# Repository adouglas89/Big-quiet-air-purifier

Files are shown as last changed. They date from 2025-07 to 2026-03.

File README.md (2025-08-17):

# Big-quiet-air-purifier
Big Quiet Air purifier/filtration machine, can be remotely managed/monitored, very high performance to cost ratio.
This uses a large axial fan with unprecedented flow to noise ratio at the pressure of concern - about 4-6 pascals, which is not much pressure.  It also gets relatively good flow at higher pressures for the noise, but you want to keep in this region if you can for highest CADR.

This system uses standard furnace filters, which are available in a wide range of MERV ratings, and even HEPA, in the same size and shape.  You can sub in whatever you want but probably there is a MERV rating that gives the best CADR.  It may or may not be MERV-13, but that's a good starting point.

The fan currently requires a large format printer.  Don't buy anything Tronxy, I can tell you that, they are the worst machines I have ever encountered and the company won't send you spare parts etc either.

Everything in this repository is going to go out of date as things are changing fast.

Actually making one is something that will become easier as the development is sorted out better.  If it's confusing that's no surprise, manufacturing is never easy, people don't respect it for some reason but they should.

The CAD files for the big quiet fan will also be integrated into this CAD file from now on.  The files in the repository specifically for the big quiet fan will eventually be obsolete unless I update them.

here is the bom: https://docs.google.com/spreadsheets/d/1DK419Db4-yF4lkq_DYZrtrG0oX9ysA3eVCCv0GqU3Kw/edit?usp=sharing
it is changing rapidly so I don't really want to upload it as a static document, and there seems to be no way to have a spreadsheet on github.  When things stabilize I will put it here.

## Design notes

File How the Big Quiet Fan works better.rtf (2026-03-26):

This document is to answer the often asked question of how/why the big quiet fan is so quiet.
● First of all the actual details of curves and polymers are not the whole story
○ The incentives surrounding the project
■ Lack of asshole boss rushing me
■ My own desire to make stuff that’s really really quiet, and do a good job to prove my abilities in this regard. I want it to be beautiful.
■ My reputation in the community and with the funding organization was an important motivating factor I guess.
■ A focus on sheer performance rather than appearance or manufacturability in the early stages. In fact sometimes noise is considered beneficial because people perceive something that’s louder to be more powerful. Obviously dispensing with that kind of pandering to ignorance is an easy way to make progress on performance. I also rejected the idea that it must be cheap. The *ratio* of cost to performance is much more important. In a way both of these and much more comes to making a wise objective function early on and allowing that to guide development efforts. The whole thing is one big optimization effort.
○ The methods I have employed including optimization, actually building prototypes, working with good efficiency are important. Both in terms of getting on with things faster and sooner and also with less money and space. With a fixed budget, higher efficiency will give a better result.
■ Prove the most uncertain stuff first. That was the blades and then the ability to print them with reasonable efficiency. Then the motor/driver comes after. That way if you have to change course you have less lost effort.
■ Obviously basic engineering fundamentals apply, like using modules that others have done a reasonable good job on wherever they are adequate.
○ “Forever modular” is useful, keeping the door open to improvement well after I thought I was done.
○ Keep orderly notes and data, I don’t think paper notes are really up to the challenge. You can’t make a spreadsheet on paper. This is important to remember and refer to what worked best, so you can mix and match the best features during the optimization process. And also if something goes wrong you can figure it out better.

I also spent some time relatively poorly, because I was working towards serial production through additive manufacture. So this whole project did take longer than it would have if I had been able to plan ahead a little more effectively. However to be fair I see supposedly much more experienced people doing very similar things with far lower efficiency. Also exploration is kind of like that, you can’t know what’s ahead, that’s part of the program.

One thing that was profoundly missing was collaborators. That would have helped a lot. Except the funding was in a way a form of collaboration.
This could have been done in some kind of community space, but you’d need some space of your own, and the freedom to run the machines overnight etc. Being able to work in my home was useful on a technical level but I think quite a problem psychologically, as you tend to have problems sleeping and waking when working and sleeping in the same relatively small house (even a full sized house, which I had for a while).

It would be a good idea to also discuss what did not work out as well, some of this will be implied, some included after.

Some people will say this is too much detail, but when you go to make a variant, it’s not going to be too much.

What is the general technique employed here?
● The general idea is to first do the best we can with simulations, then build a test rig and then try various fans with a reasonably intelligent approach (better than brute force) to see which gives the best noise and flow/pressure. To simplify things, I picked one RPM, 300, and optimized to get better results at that point. Now I’m usually using 400 rpm because it’s quiet enough at that speed, so optimizing again for that RPM might yield improvement. Unfortunately this is not actualy that easy as the only practical way to know how much noise one aspect is contributing is by eliminating it. So the motor for instance, you have to make that quiet before you can get far on the blades.
○ The optimization process involved binary searches and also looking in there with smoke etc. to see how the air was flowing around, listening to see if I could determine how the noise was being produced (easy to tell motor hum or blade buzz from the whoosh of the blades due to turbulence for instance). Then forming hypothesis, proving them and testing more.
○ I make at least 52 unique prototypes, I think. Some were not documented as they were uninteresting, like the one with the slightly defective frame that made a surprising amount of noise as a result. By this I mean I often recycled parts to make new fans, including mixing various primaries and secondaries to see what worked better. Different spacings between primary and secondary were also tried but I’m not including that in the total of 52. There must have been hundreds of exact unique combinations tried. The most important thing to document is when progress is made, but documenting everything is probably a good idea, as long as you can still find the good stuff.
○ Obviously, back the best stuff up periodically and keep an orderly workplace etc.
● It’s also useful to note that MERV-13 filters may not be the optimal at these pressures and for these configurations. There may be a significantly better filter/geometrical arrangement combo. You’d have to go back and forth testing and improving both to work your way to a better air purifier if you wanted to optimize for both 400 rpm and different filters. I used 10x merv-13 filters with the VVV in the middle (see bqap builds document).
● A primary blade that is relatively thick. It imparts pressure to the air, and also rotational motion. The pressure is directly useful, the rotational motion will be converted to pressure to some degree by the secondary. Usually it’s just about pressure. The thicker the blade disk (the cylinder around the blades) the better this works, but of course it’s a practical compromise with how large you want to let them be.
● A secondary blade, also called stator blades, which are stationary but the air is rotating relative to them, at a lower rpm however, than the primary relative to the air entering the fan.
● The primary and secondary are curved oppositely to each other, that is the spiral in the xy plane is opposite handedness. This prevents the pressure wave emanating from the primary from slamming into the secondary all of a sudden, which produces a buzzing noise that we don’t want. Many fans use struts that curve for this reason.
○ The struts on some blades are also flat and slanted to reduce their cross section in the direction which the pressure wave propagates. The secondary blades are to some degree like this automatically, although they can’t be minimal cross section of course. But they are a lot better than flat bars.
● The blade number and curves of the primary and secondary are different, the de facto rpm is different so the optimal isn’t likely to be the same.
● Spacing between the primary and secondary turned out to be important. Early prototypes did not work well as the spacing was too large.
● The thin wall on the outer edge of the blades is not strictly that helpful from a noise standpoint, I think, but it is important structurally, allowing the blades to be thinner, and thus easier to print and mold. It also prevents them from flapping around, but to be honest I never tried any variants without it so I don’t know the impact it’s having for sure. People think it reduces tip vortices, but I don’t think that’s likely to be a major factor here, that’s more of an issue at higher blade velocities.
● The spiral curvature (xy plane) and zy plane curvature of the blades,blade number for both the primary and secondary, thickness of the blade disk (thickness of the cylinders that surround the primary and secondary blades), hub diameter had to be adjusted to find something reasonably close to optimal. Diameter was fixed but in another application you might want to optimize that too.
● The grille has to be adequately far away from the primary blades, otherwise it creates noise as the pressure waves slam into it. This is why it’s not directly against the secondary, or integral with the secondary. I found it had to be a separate component, which is unfortunate as it costs more. Of course it can’t be too dense/thick elements as that would impede airflow, too. Making it further away from the primary also reduces the density it has to have, allowing air to flow through it better.
● The polymer turned out to be important. By coincidence I found some fans were quieter than others, and since I kept good notes (this is important, keep orderly notes and data) I was able to identify that it was the polymer used.
● The motor/drive solution:
○ After realizing that stepper motors do actually have the required speed/torque characteristics, which is hard to get from other motors at a good price, I pursued the use of a stepper motor as a practical power producing motor
○ The previous motor was an 11 pole pair motor. A typical stepper is 50 pole pairs. They are also bipolar rather than three phase. Aside from this, driving them and their noise characteristics don’t have to be that different
○ Everyone thinks steppers are inherently noisy and this is not entirely wrong, because of the high pole pair count. However whichever motor I use I would probably want vibration isolation, so if I have to isolate the stepper motor this isn’t that big a deal.
○ After realizing the drive strategy was working particularly well, I tried to eliminate the buzzing noise with anti cogging. This did not go well. I spent along time on it and got basically nothing for it. It is not clear to me why it seems to be practically impossible to drive the motor with very little torque ripple. I think it may involve some kind of excited oscillation. There seems to be no electrical waveform that can be fed to the motor that leads to completely smooth motion.
○ Therefore I decided to just suspend the motor so it can produce torque but the vibration is isolated. This is inconvenient and adds cost, but again probably any motor would require something like it to some degree. Going to town with it is not a whole lot worse than a little bit.
○ The motor turned out to vibrate due to some kind of feed back loop combined with some harmonic resonance. It was so severe that when allowed to vibrate due to the decoupling, it would stall at some speeds. To dampen this, I added a flywheel made of a high damping polymer, 95A TPU. I had some difficulty getting it to transmit enough torque, but eventually solved that. This appears to reduce the oscillations at an even lower level. This is what makes me think there is some kind of oscillation that is excited and part of a feedback loop. I’d have to figure out the physics and math out a bit better to elucidate this (see where the gain coomes from eetc by modelling the system basically), but for now it works fine.
○ The drive strategy is particularly curious. It’s not actually open loop as we know it, there is no actual current regulation. It’s only ramped voltage. It works because the back emf goes down when the torque angle increases, which it increases with load. If we apply a constant RMS voltage, thus the current actually compensates for higher load automatically. It just has to be in a suitable range for the rpm. It could almost work without this, but having it is particularly helpful as it further increases safety margin against stall.
■ There is a system in the driver for the more recent programs that uses a polynomial that predicts (measured) normal operating current. If operating current is outside the range predicted, it shuts off themotor. You have to power cycle it to resolve the situation. In other words you need the user to come pay attention, which is what we want. If someone shoves something in the fan, it therefore shuts down automatically. If it stalls for any reason like a wiring error, this system also trips.
■ Thi strategy is mentioned in some old textbooks but I haven’t sen it anywhere else. I would simply describe it as voltage ramped synchronous drive. Not open loop, open loop implies current regulation most of the time.

It’s worth noting that it’s probably possible to improve performance slightly further by further adjusting the curves and blade number, thickness of the blade disk, hub diameter etc.I am not immune to the reality which probably led most other fans to not be very good, which is that you have to get on with actually making them at some point, and there is not really that much good reason to exceed the requirements set. That would be ASHRAE 241 for the amount of clean air we need in a classroom and other buildings,and ANSI S12.60, for noise in classrooms (hospital wards and other spaces have similar standards which have mostly similar values anyway). This fan can already be used to make an appliance that can do that with only one fan, while everything else is a long way away from that.

Because things are modular I could change things later to pursue this improvement, if/when there is a good enough reason and funding.

What did not work very well?
● The rings similar to the outermost wall, I had some in the middle regions too, and they added a lot of noise. They did improve the flow/pressure to rpm ratio, though, as predicted by simulations. I noticed from the simulations that the pressure/flow was better in the regions close to these rings, so that is why I added them. That was correct. But the simulation did not show the increased noise.
● I tried using a tpu/nylon blend to increase damping, just for the primary, but it made no difference so I went back to the previous approach. I thought it was going to help as the difference in damping between some rigid filaments did help. It might help for the secondary more, but it’s a little too floppy, it was 72D durometer. 100D might work ok but I couldn’t get any. You can have high damping while still having high stiffness, there is nothing stopping that. It’s just that TPU has good damping and is usually used in elastomers. There are some papers that describe filaments with unusually high damping but you can’t buy the filament of course.

Things I did not try
● Multiple rotors, separated by stators to reduce the rotational velocity of the air. This would increase cost and it actually can get complicated because the bearings can make noises etc. which can be solved but it takes more time and the per unit cost would go up. A single primary and secondary is a reasonable compromise.
● One thing that has some potential is airfoil shaped blades, i.e. the back of the blade has a different curvature than the front. This would be easy to do with printing but it makes the blade thick so with molding you’d end up with heavy blades and using a lot of plastic. Contraction could also be a serious problem. You could try to make it in pieces and assemble them or something. But that’s expensive. For this reason I did not explore airfoil shapes much. I did simulate some and it didn't seem to help much so I didn’t pursue it.
Things that probably don’t matter much
● Some people think the ridges on the sides from the printing must have an impact that is detrimental. I think this is unlikely due to the boundary layer, especially.
● I tried slanting the outer wall a little but it made basically no difference. I may do this again when designing for manufacture as it should make removal from the mold easier.

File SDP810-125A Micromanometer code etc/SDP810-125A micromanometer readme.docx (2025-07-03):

Check out the datasheet for the sensor, it says it’s pretty good.

Shop around before you buy, some places have it a lot cheaper, like half the price of others.

This is a simple system to read the sensor over I2C a bunch of times, then calculate the average and display it on an LCD.

It’s made for a raspberry pi pico. You will find the pin numbers in the code, remember they are GPIO numbers not physical pin numbers.

Note that the sensor actually has a small hole from one side to the other, this is a very important thing to know, because if you use a long thin tube to the sensor, the apparent pressure will be reduced. It remains largely linearly proportional to the real pressure but you gotta be aware of this phenomena. If you want a good reading use a short wide tube on the sensor side. A 380 mm long 1 mm ID silicone tube reduced the pressure reading by a factor of 3.5, approximately.

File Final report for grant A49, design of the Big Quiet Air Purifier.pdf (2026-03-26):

# Final report for grant A49, design of the Big Quiet Air Purifier

Overview:
This project went well as far as it was taken, however we terminated it early to roll the funding that remained into the Big Quiet Fan mass production. This is because it became apparent that the taped together air purifiers actually work quite well, and the other aspects that differentiate a BQAP from a taped together assembly (which I dub an Extra Quiet CR box or EQ-CR box) are not really that important, but at the same time are costly.

However, the anemometer and the internet of things control box were a good success. Secondly, I did learn a lot which I do plan to eventually hopefully apply to build additional prototypes, and if the market is amenable, to sell alongside the big quiet fan, however it doesn’t look like a low hanging fruit.

One finished air purifier is now in operation in a classroom at the University of Waterloo. A second one is a Cite Des Hospitaliers, a coworking space, in Montreal. A third is at Foulab, a hacker space in Montreal. A fourth was located at a social central called Lachoppe, but they foolishly threw it in the trash, an absurd thing to do, illustrating that the machine alone will never be enough, anti-propaganda is important as well.

The school board of Connecticut has apparently funded taped together CR boxes for all it’s 40,000 classrooms, at about 11.5 million USD or something, so apparently taped together boxes are adequate even in that sensitive context. Thus, focussing on the fan seems like a good first step.

I developed solutions for the physical structure, holding filters of various sizes with the same physical structure, and getting a large number of filters integrated into the machine to reduce pressure drop. I developed the 6 filter internal V box, which nobody else seems to have thought of before but works well, and is in general the winning configuration. Even a good solution for the handles at the corners is done.

I hope to use extruded aluminum in the future as the wood was of marginal strength and appearance.

I realized that because of how the details stack up, adding more filters generally decreases the cost per cubic meter. I realized cost per cubic meter is a good way to think about things.

I developed a good approach to a cosmetic cover, and have ideas to improve it further. Solutions for tamper proofing were also found (durable yet low cost grilles and also mounting it high up). I have ideas for putting the fan in pushing mode to further increase CADR and mounting it near the ceiling to leverage displacement flow.

Concepts for embedding the whole system in a false ceiling are interesting.

Budget:
Total budget was $30,000. Not quite all of this was expended. This may indicate that it would be a tight squeeze to make 30 units. However the plan was supposed to be to actually sell the units so that part would have been mostly self funding. I think I struck a pretty good balance.
| CAD | USD
labor cost | 25060 | 18159.4202 9

sum of all
costs with
labor | 31072

22515.9420
3

Estimated impact
The designs are published, as well as some information about the general lessons learned. The filter configuration with the diagonal internal V and 6 filters is applicable to taped together boxes, allowing increased performance while also reducing cost.

Once we have a good supply of the critical ingredient, the fans, it will be time to pick this up again, or perhaps someone else will. There are a number of examples of entrepreneurs making kits for air purifiers, and this both builds upon and enables that further. I have offered Northbox a sample control box and anemometer assembly so he can make his air purifiers remote controllable and monitorable (including the filter cloggage levels).

Many users will not be happy with taped together CR boxes, so this is a good start on a good option with the same net performance, albeit at a higher upfront cost, and with the same great low running costs. Filter changes are easier and the finished assembly may be possible to get UL listing for, encouraging uptake in hospitals and other tightly regulated spaces.

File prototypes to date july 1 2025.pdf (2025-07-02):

# 10 Filter filter box (“CR box”) with Big Quiet Fan experiment/mock up(s)

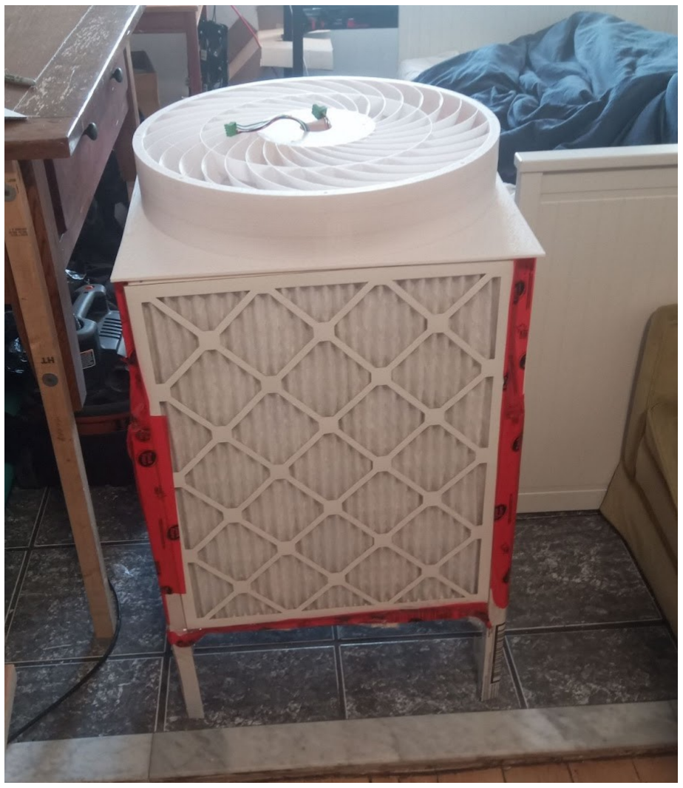
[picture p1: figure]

Update march 5 2025: This device uses an older model of fan. Considerable progress has been made. It’s been in operation all this time and working well. I added a safety feature, a thermal switch, but it hasn’t tripped even at full power. During summer at high ambient temperatures that could still happen. The safety margin is a bit slim on that count, but the safety margin against actual overheating is good. Remember this is all only proof of concept, mostly about the blade design and the filter arrangement, to prove high CADR to noise ratios and high cubic meters of air to total $ expended (10x or more higher than the next best, 30x or more than typical air filter units). Also the estimates for the boxes in this document may not be very good, regarding flow rate etc. There were a lot of sources of error back then, they were only estimates. These filters are also on the crummy side, lower flow rates than filtrete ones. I have since build a better box and it works well. I will build another in due course, but I may return to these crummier filters because they are half the price and that’s pretty important. I have also measured a very similar system precisely with a validated anemometer. The latest fan gets 1452 CFM measured precisely with the validated anemometer, at full speed, 400 rpm (47.5 dBa) with 3m filtrete merv 13 filters, and 1111 cfm at 300 rpm (37.5 dBa). That’s flow, not cadr.

Edit: to be clear, this fan is 3d printed. It’s source, the cad files, are available at openerv.ca as well as information to help you get the rest sorted out. However it unfortunately requires a large format printer. Don't get the veho-600 it's terrible, or anything tronxy. The orangestorm from elegoo looks good.

# Intro

I have been working on a window-fan sized fan with the best flow to noise ratio through a set of merv 13 filters I was able to arrange reasonably, as a proof of concept that it’s possible and practical to do far better than we have been doing.

I also thought up a way to cram 10 filters into a filter box of nearly the same dimensions as a 5x or 4x box. It has to be lifted up off the ground with legs, like a 5 filter box, rather than sitting on the ground, but that vertical space is not usually used anyway.

The sides should stick out a little more than a 4 filter box, just a few centimeters on two of the sides, to improve flow on the interior of the box. I just made it a square instead, so it sticks out on all sides, to keep it simple.

Edit: move the triple V down some too, that should help.

You might even be able to up it to 12 filters with a quad V.

The key to realizing why this is a good idea is that the cost per cubic meter does not go up when you use more filters, because you get x amount of air per filter before it’s “clogged” either way. Or rather, X amount of particulates, and the air passing through in this context has already passed through and thus has very little particulates in it.

But when we have more filters, we can turn the fan down and get less noise for the same flow rate. Efficiency of particle removal might even go up as velocity through the filters goes down. The fan can be lower power, which is cheaper. Fitler changes are less frequent because each filter captures a lower fraction of total particles the machine intecepts. It’s definitely a win, except that the upfront cost is of course higher for the larger number of filters. Except now we can use cheaper (about half the price) generic filters instead of the good Filtrete ones or whatever, and still get pretty good performance (the cheap ones do have about 1.5 times the pressure to flow ratio). Also sourcing filters becomes easier for a given performance.

Edit Dec 10 2024: Actually, I think the cost per cubic meter may actually go down when we add more filters. This is because you have a pretty high ACH with these appliances, thus almost all the particulates that can clog the filter have already been removed from the air that passes through the appliance. It’s about the particulate matter the filter intercepts, not the amount of air that passes through it, that determines how long the filter lasts before it must be replaced (assuming a given flow reduction is acceptable). But because the particulates released into the room to do not increase when we filter the air at a higher ACH, that additional ACH is relatively cheap - nearly free probably - in terms of filter cloggage/cost. Secondly, though this is not additive or multiplicative with that but could become prominent in some contexts: suppose you need a CADR of X. You can get more particulates intercepted per filter if you have more filters, because each one can clog more before it passes the “time to replace it” threshold, because the sum of all the filters flow is the cadr. Thus if you have twice as many filters, each one can suffer twice the cloggage level (half the pressure to flow ratio) and still be serviceable in an appliance that gives X cadr. Thus, you can extract more filter life per filter if you have more filters, all else being equal. Thus, the cost per particle intercepted or per gram of solid matter removed, actually may go down with more filters, all else being equal.

So, increasing the number and density of filters is really the way to go, pretty much a win all around, all else being equal it’s going to make things cheaper and quieter for sure, the only downside is it increases the sticker price of the assembly, course. If we assume a certain interest rate on the cost of the filters because we need to buy them today rather than in a year from now, the cost of the expenditure is very small compared to the benefits that accrue along the way. It's a very good investment. So rationally, it's really the way to go. Exactly how much so warrants a spreadsheet to reckon.

You want to try to use the wells-riley equation and some similar approximations to calculate the cost per infection prevented for various appliances. The cost will change for different contexts though. What we really want is an objective metric that calculated the cost per qaly gained, with weighted average calculated for a wide range of scenarios the particular machine is intended for. You would subject each machine proposed to this evaluation and pick the best. I think this fan combined with very dense large filter like this would likely be a winner by a large margin but it would be nice to actually check this quantitatively.
– end edit

In the case where you simply tape together 10 filters, it has the added benefit, and also in other cases, that you, at a flow rate of X, do not need to change the filters as often. Indeed <1/(2.5) times as often, as compared with a 4x box, if we assume they need to be replaced after each filter intercepts x many grams of particulates, and total particulate interception rate is
unchanged. We may get more than that because the particulate loading per filter that is acceptable may be higher in this 10x config. Since we have to tape together a new box every time, we’d appreciate this long lifespan. Estimating filter life is difficult but some studies indicate a 4x box had no problem after a year of continuous operation so we might get like 3 years, I don’t know. The degradation of the electrostatic media could be a factor at that time scale. What we would ideally talk about is grams of particulates intercepted vs the CADR the appliance gets, and then have a cutoff at say 30% reduction from the new state and see how many years that is. Then we could compare various configurations more directly and reliably.

This box is a big one but the concept can just as well be applied to smaller boxes, you can get filters down to 8 inch size even.

The key is the triple V in the middle, you might even be able to make it a quad V, but I figured this was a good start.

When using crummy generic filters like these, it is particularly valuable, as they impede the airflow considerably more than good quality filters.

I have estimated the airflow with my Big quiet fan, by covering most of the filters, to increase the pressure, measuring the flow rate through the filter with my anemometer, calculating the CFM per pascal, and then extrapolating to the situation with 10 filters uncovered (the pressure is also measured with the same sensor in the 10 filter context).

The net flow rate indicated by the instruments was 1475 CFM. If the efficiency is 0.8 then we get a CADR of 1180 CFM. With a noise of 40.6 dBa, according to prior measurements of the fan at the same RPM (300 rpm). However I suspect my anemometer may be reading a bit on the high side. I am looking for someone with more sophisticated test equipment.

It occurs to me you could replace one side with another fan. Basically you are condensing 2 to 2.5 filter/cr boxes into one, approximately. Not a bad trick really.

Steps:

First we are going to make the legs out of cardboard. I tried to make them right angle triangles but my precision was a bit poor and I think square might be better. Cut strips of cardboard about 500 mm long and 15 cm wide. Then fold them along the corrugations at three lines spaced equally apart with a straight edge, and tape them. I forgot to take pictures of this step but it’s pretty straightforward. Mark the stuff with a straight edge and

marker then cut with a box cutter.

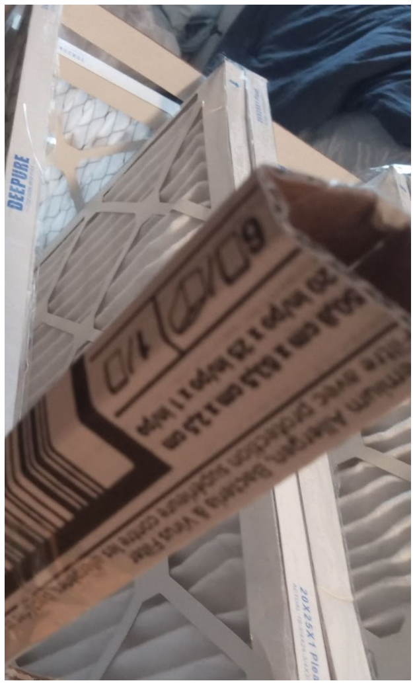
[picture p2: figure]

Mark the legs at about 200- 250 mm, but all in the same position from their ends, with the marker, we will use this to help position them later
Tape the peripheral box together, I went around with the tape, attaching the filters and legs at each corner successively. It helps to put a bunch of tape pieces on a nearby table so you can hold stuff with one hand and grab tape with the other. Don’t worry about sealing anything yet, we get the structure together first and then we seal stuff.

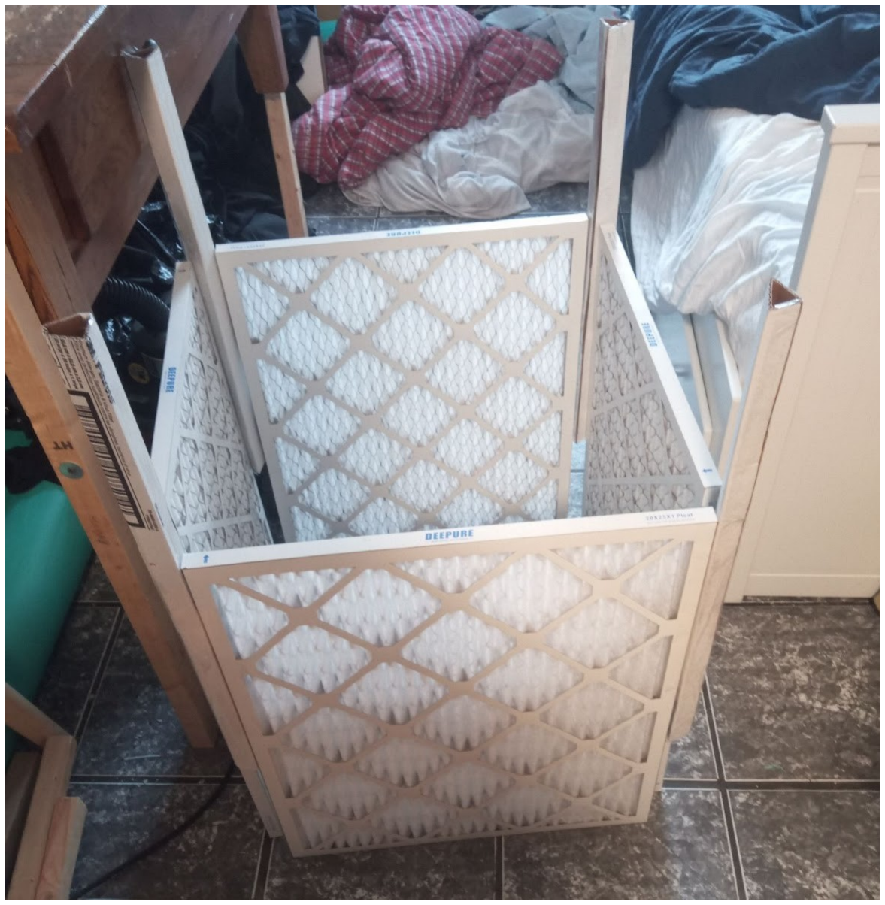
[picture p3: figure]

Next, we need to prepare the triple W insert. Start by arranging the filters in the right way, the arrows to indicate direction of flow should be right. The outer two point outwards, then the ones in between alternate.

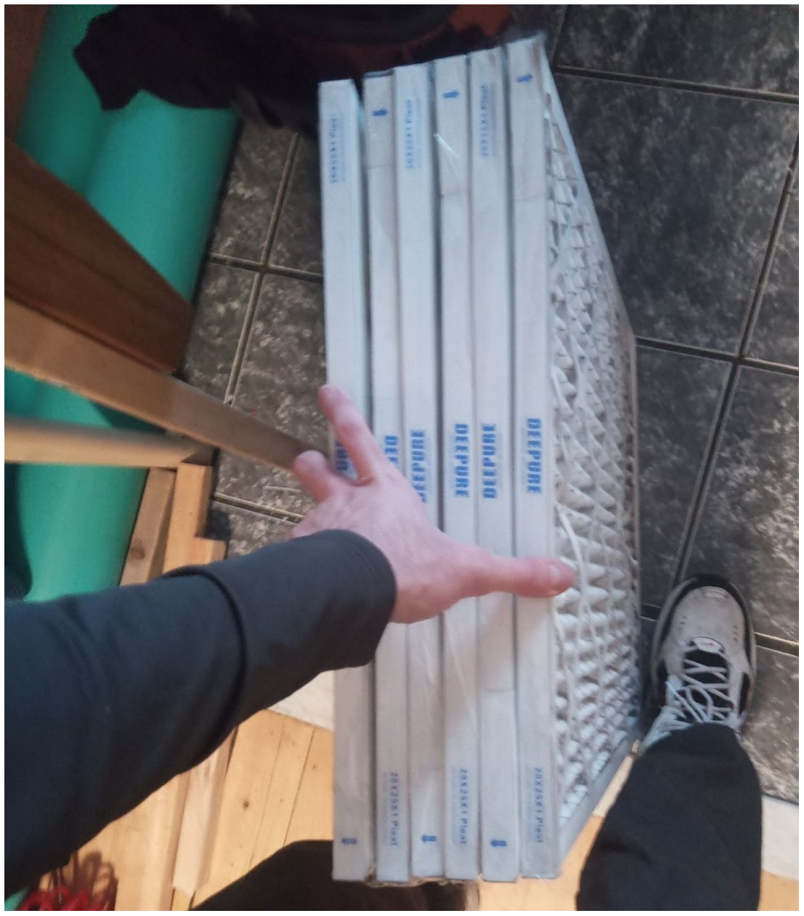
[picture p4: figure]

Just tape all the edges together, don’t worry about which ones to tape and which ones not. The edges of the tape stick anyway. Just tape it all up and then cut it in the right places with a box cutter. I then attached some strips of cardboard to hold things in position. Measure it against the nearby square box thing to make sure the VVV is the

right width etc.

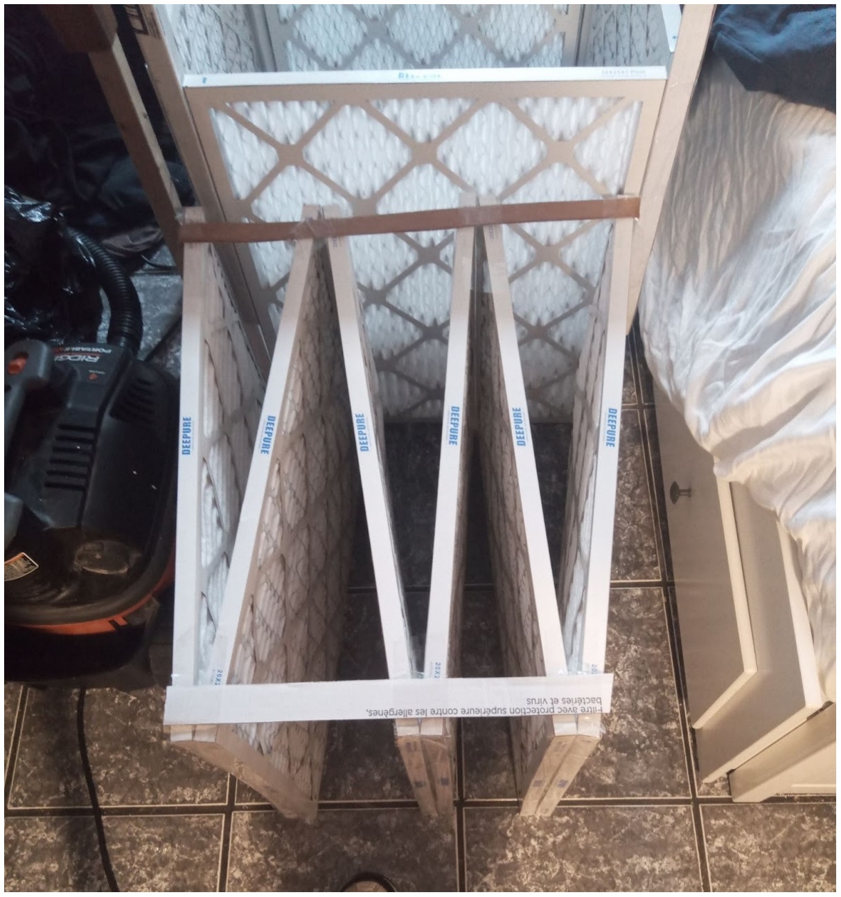
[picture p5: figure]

Next we block off the relevant areas in the Vs with tape. On the wide end it’s going to stick out so the tape doesn’t have to extend to that area

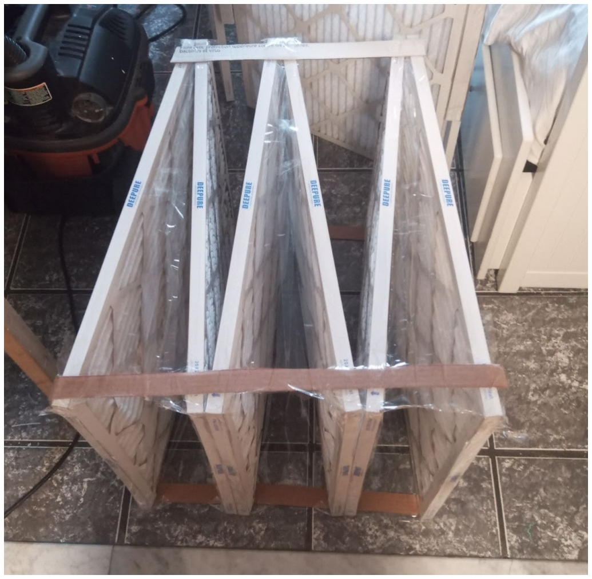
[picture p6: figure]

Now we can insert this component into the peripheral box to make sure it fits. But we want space at the end for air to flow, so I’m going to back them out a bit, whether this is necessary I don’t really know.

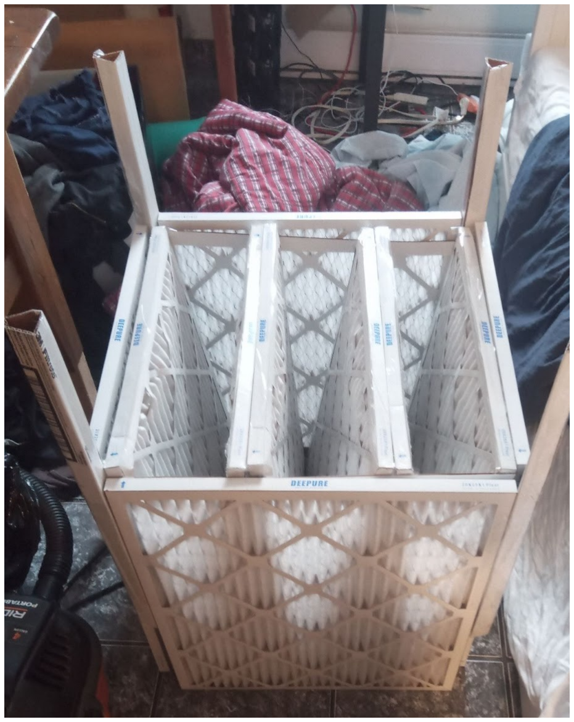
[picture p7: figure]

Tape the triple v thing in position and then seal around it. *notice that it is not flush with the bottom of the peripheral filters*. This extra space is important for air to flow around.

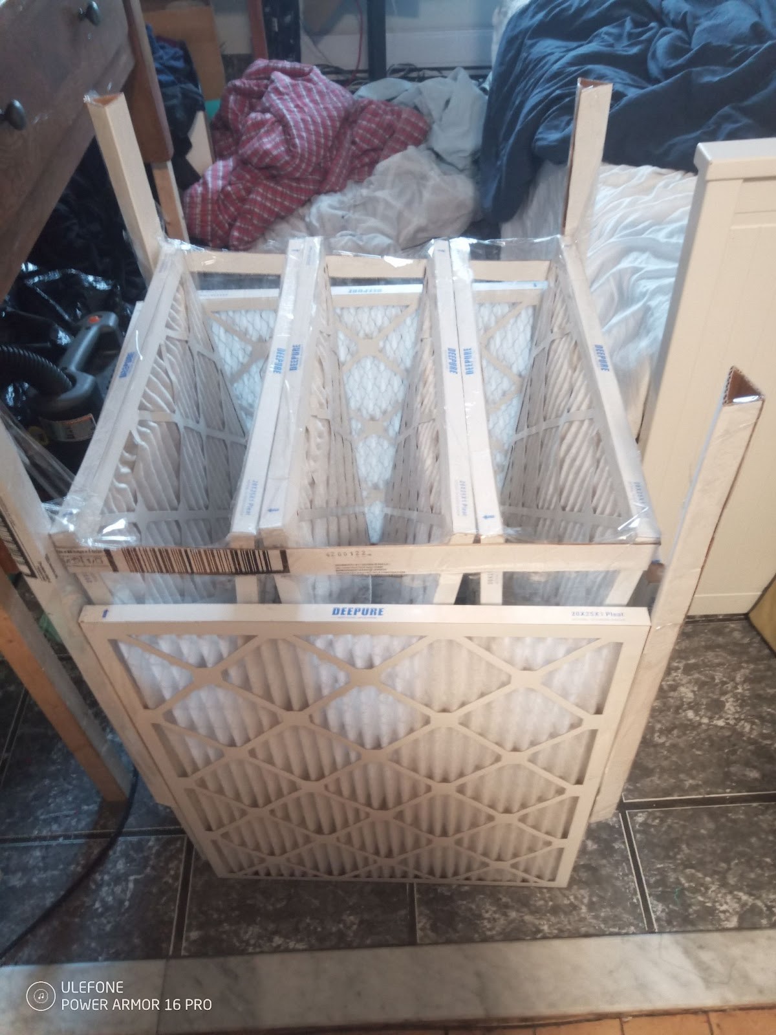
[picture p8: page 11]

I would increase it next time.

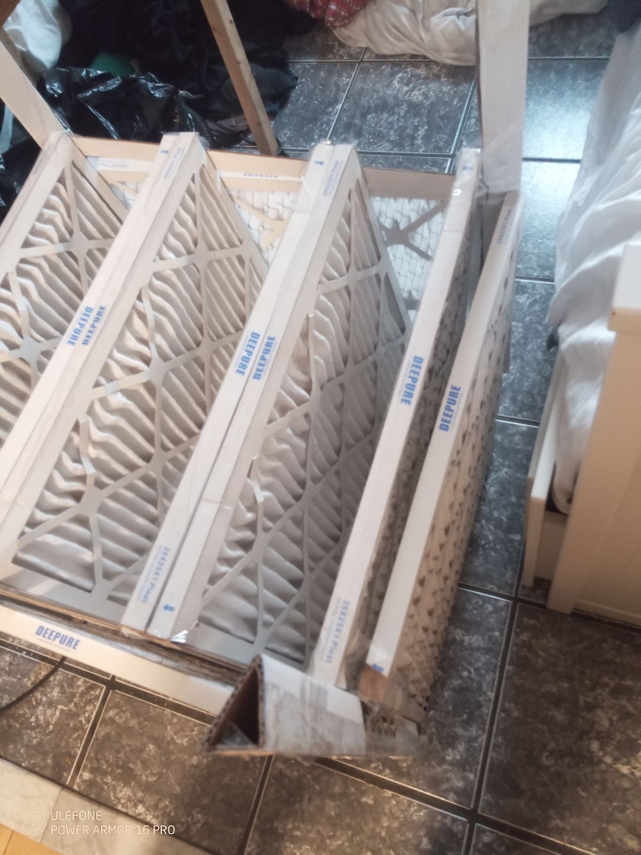
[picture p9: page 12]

Hard to see the tape in the pic but I ‘m pretty sure this one is sealed.

Now you can turn it right side up and if necessary, trim the legs so it is level. Oh and tape the rest to seal it. I ran out of packing tape so I used tuck tape.

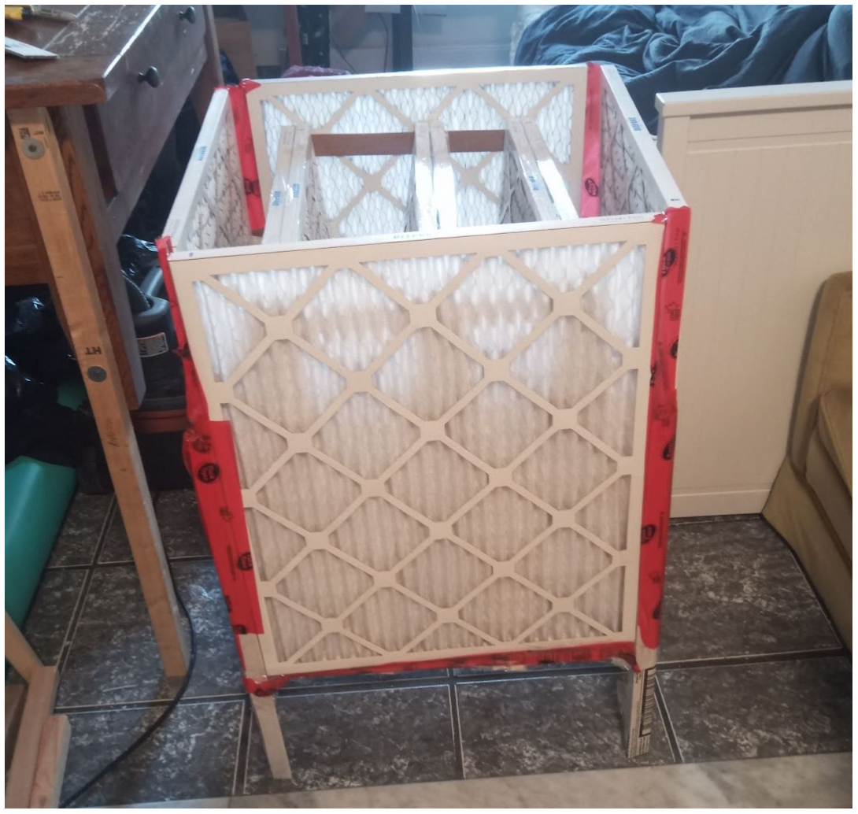
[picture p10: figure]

Now you can simply plonk the fan on top, I am not taping that to seal it because it’s just a test. This fan shown has no power supply attached, I’m just showing it. Again, this particular box is quite big, very large capacity, but you can use the same general pattern

for a much smaller box.

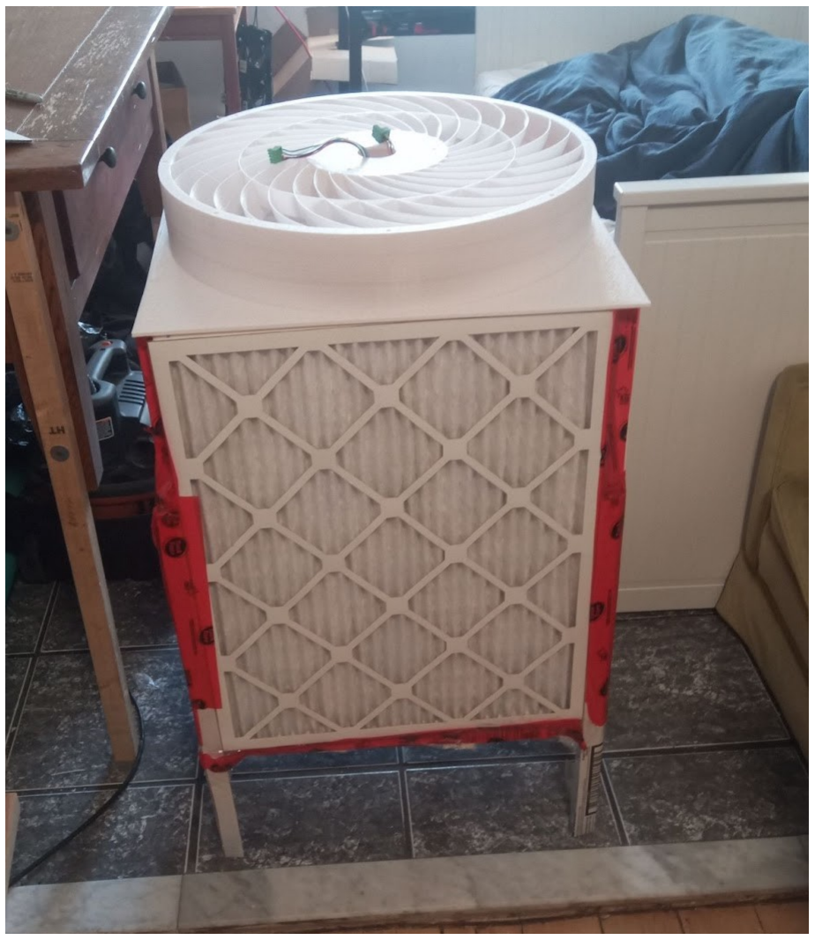
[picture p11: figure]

This filter box has now been assembled and installed and been operating at Foulab. Someone kicked the leg apparently, the cardboard legs are not a good approach, they should be timber, hanging it from the ceiling or putting it on a table or something would also be a much better idea. The next one I put on top of a fridge.

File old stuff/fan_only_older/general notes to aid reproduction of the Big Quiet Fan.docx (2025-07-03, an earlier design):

The motor I used is the DCH-6829F motor from JD power.

This is a good choice, it’s a bit expensive but works well.

Little coggy for my liking.

The best so far as of feb 13 2025 is the version 16 primary combined with version 10 secondary, and about 3-4 mm spacing between them. The version 6 frame can be used, the frame in the v10 or v16 files should also work fine, they are almost the same and should be compatible.

At 390 rpm with version 11 primary and version 10 secondary, with 4 mm spacing between them for ten minutes, the motor was 50 degrees C, so definitely a bit warm. Probably higher powers are not practical.

I tried a smaller one and it wasn’t abe to provide the torque. The higher the airflow for a given rpm the higher the torque of course since air power is similar, so we are generally looking at pretty high torque.

I used rubber orings, 3 mm silicone rubber (2.5 mm id 3mm thickness), and also tried rubber washers and some silicone gel pads (made for damping cymbals, easy to get on amazon, cut them up and poke a hole in the middle for a very squishy washer).

I chamfered the holes near the silicone orings with a drill bit, this also helps as it holds the bolt in the center of hte hole. An oring goes on either side of each through hole, so there would be 16 orings in total (2 on each side of 4 holes). There needs to be a washer under the head of the screw to contain the oring. They are M3 screws.

**do not use screws that are too long, if they go through and hit the coils of the motor it can break the coils and destroy the motor***. Be very careful about this. The orings compress and the screws stick in to the motor more than first appears. Use washes under the head of the screw to shorten the stick out length if you have to.

Use the prusa slicer with adaptive layer slicing, and a 0.6 mm nozzle, I think 1.2 mm would work even better, the geometry is about right for that, in many areas a 0.6 has to do two roads, but a 1 mm could do only one road, and thicker layers in many areas. Could be a lot faster. I used 0.27 for the quality/speed tradeoff and that worked ok, for the adaptive slicing, with a 0.6 mm nozzle.

The high overhang areas benefit from thin layers, 150 microns is ok in my experience, for the first 5 mm or so of the primary, for instance.

Use a brim. I recommend bed weld it is a good bed adhesive.

Use an MPLA, not standard pla. Standard suffers from stress cracking and isn’t as strong. I use jayo MPLA white, it’s cheap and works well.

The driver is a B-G431-ESC1 board programmed in arduino. You neeed to install arduino, install simpleFOC and SimpleFOC drivers libraries (they might go together now) and then you can compile and upload it to the board with the arduino interface. The wiring is actually very flexible because the motor driver auto detects and compensates. If the fan goes the wrong way, switch two of the motor wires and two of the hall sensors. But they generally go in order, A is U
B is V, C is W. I forget what they call them on the datasheet/manual of the board.

Warning.: flaw discovered in motor driver program jan 25 2025, on rare occasions it doesn’t read the hall sensors quite right on startup, and as a result the magnetic field does not produce torque, thus the motor just sits there getting hotter and hotter, beware. Again this stuff is all just a prototype at this stage!

I recommend pluggable screw terminal connectors 3.81 mm pitch.

Note on actually using the fan dec 9 2024: The driver is made so that it does a sensor align, and if all is good it will start ramping up the motor to full speed. As of jan 18 2025 the voltages are about right, they can be adjusted in the program, 300 rpm is reached at about 18.6 volts input.

If the voltage is too low it will fail the sensor align because there isn’t enough torque. The B-g431-esc1 board does not operate at less than about 7 volts so don’t do that or it will fritz out and restart repeatedly etc.

The v6 fan with the spacing between the primary and secondary of 3 mm gets about 1980 CFM at 2.86 pascals, so probably about 2200 free flow, with only 15.6 watts of input power. The motor seems to be pretty efficiency and does not even get warm, if it’s 80 percent efficient then only 20 percent of that 15.6 watts goes into heating the motor. The latest as of jan 27 2025 is the v11 primary with v10 secondary, 4 mm spacing, it gets about 3.8 pascals. Hoping to up that to 4 by increasing the thickness of the blades by extending the low angle of attack region of the primary.

You could measure the coil resistance by monitoring the voltage minus back emf (have to know the KV rating of the motor precisely) to current ratio and try to detect if the motor is getting too hot. Or a sensor glued to the casing. The rubber orings also protects the plastic some. The first thing to fail when the motor gets warm would be the plastic, that would probably be the limit for long term average power.

I plan to use a ptc thermistor with a critical temperature of 60 degrees and a 5 kohm resistor across the motor driver terminals to provide protection against motor overheating in the future. Also the motor drive will include stall and overload detection (simple rpm monitoring, if the rpm gets too low it cuts power till rebooted)

I have included several .3mf files. These files are for Prusa Slicer, they contain the settings for speed and the various things like z-hop and retraction that I have found to work reasonably well. They are all similar, with only minor variations as I continue experimenting, The z hop is currently causing problems because small blobs are left which the nozzle runs into, eventually breaking the heat break and causing damage and a print failure. Without z hop it can snag on things though, the curved blades will stick up above the printing plane slightly due to thermal contraction. Unfortunately the variable layer height is not included in the files which is kind of silly.

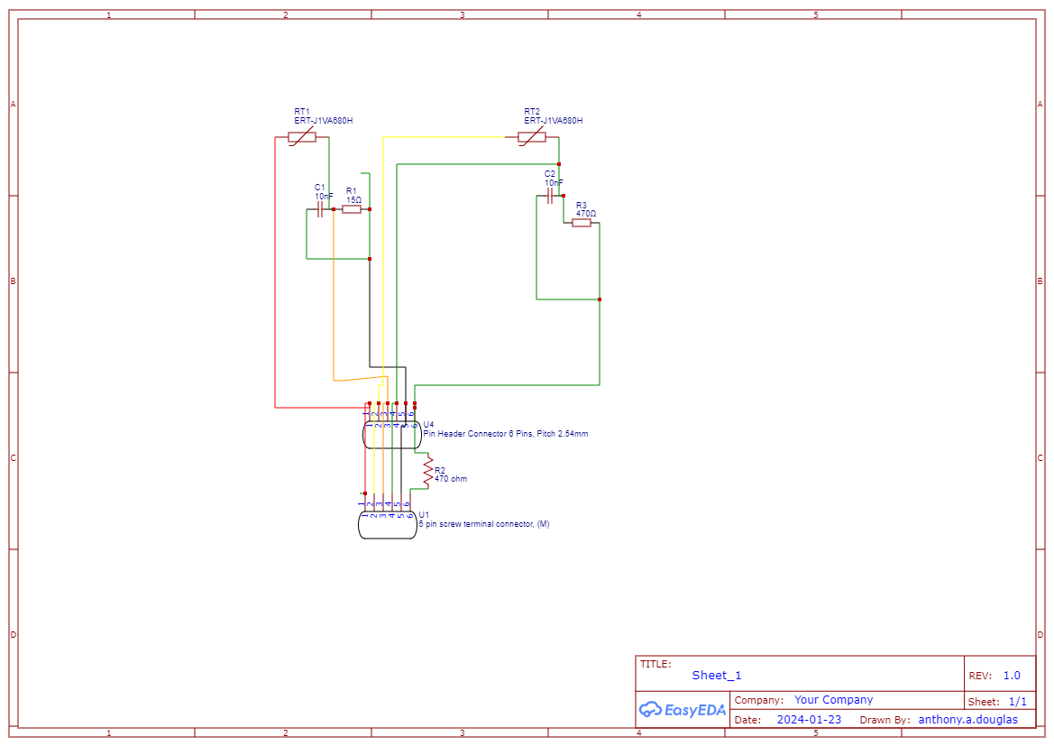
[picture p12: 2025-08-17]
small board anemometer surface mount thermistors/Schematic_thermistor-anemometer_2025-07-15.png

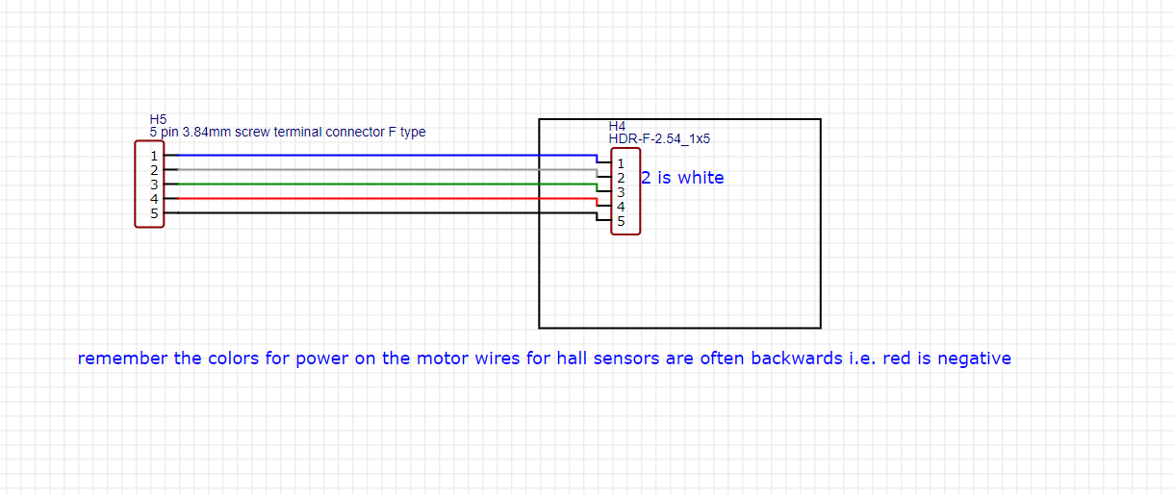
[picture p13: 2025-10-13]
driverforbigfan8vmaxjune20_2025/schematic side 2.png

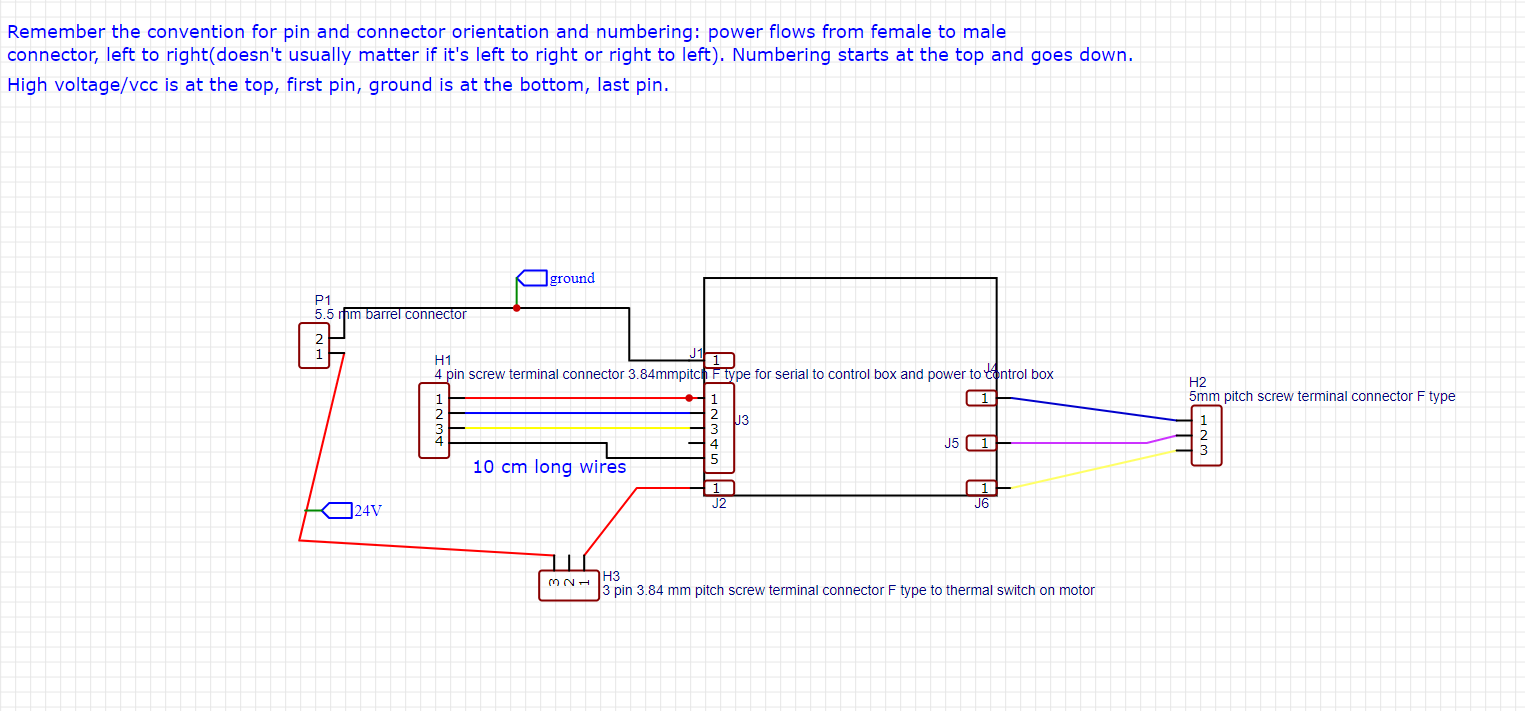
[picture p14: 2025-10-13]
driverforbigfan8vmaxjune20_2025/schematic side 1.png

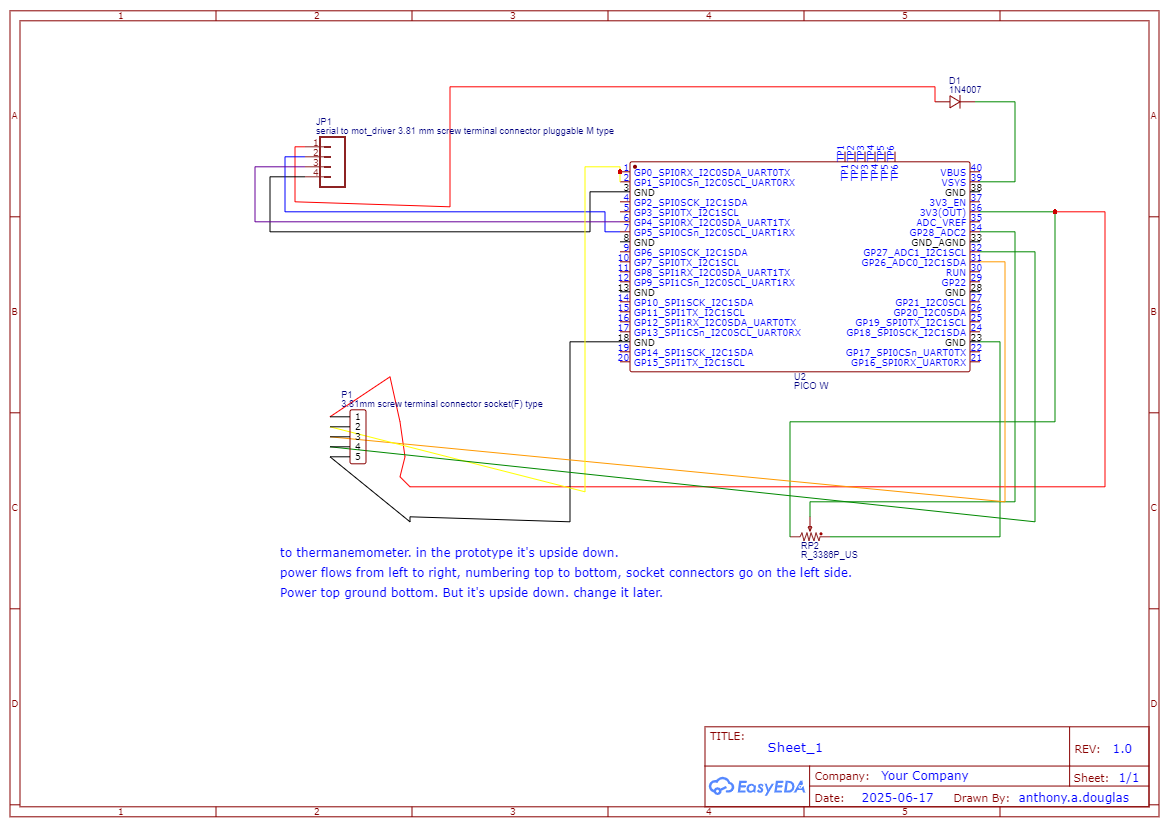
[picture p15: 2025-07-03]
control box/Schematic_control-box-for-bqap_2025-06-17.png

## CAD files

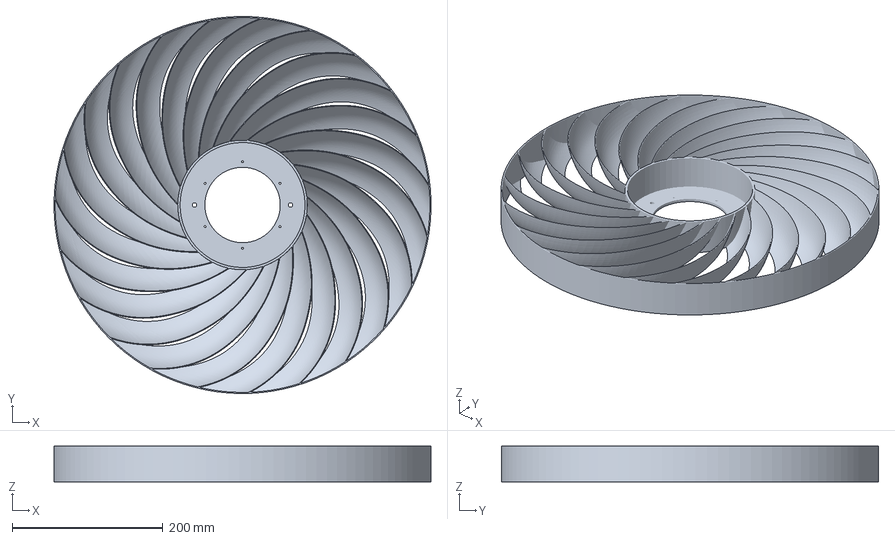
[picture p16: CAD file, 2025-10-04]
3mf/v10s_thickerwalls.3mf
500.9 x 500.9 x 47.4 mm

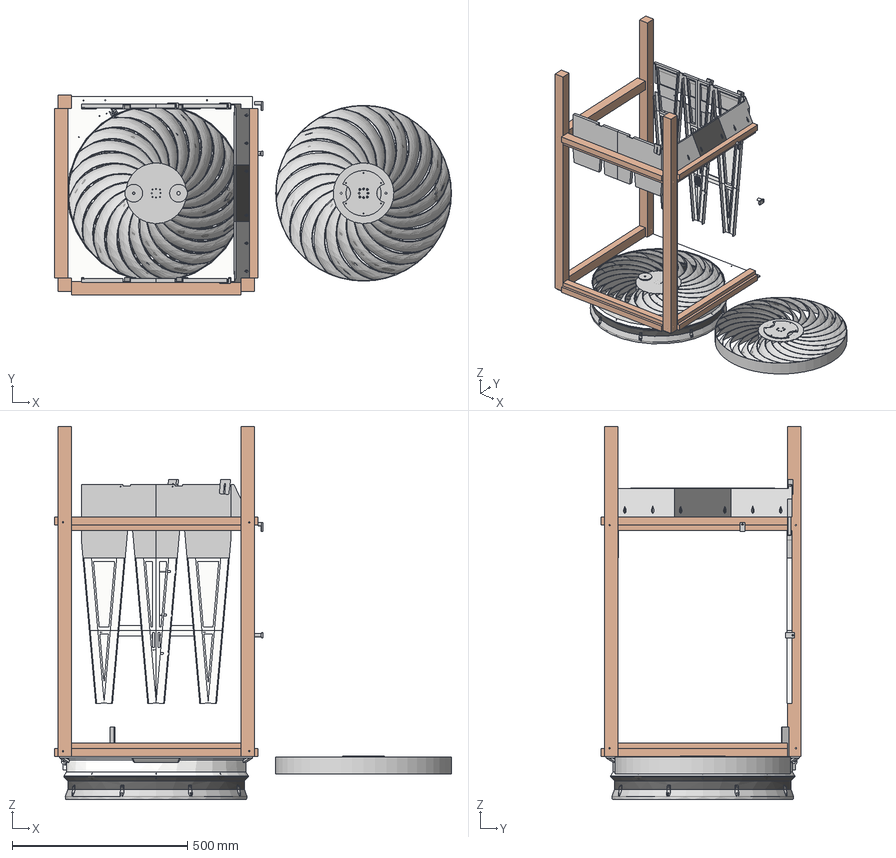
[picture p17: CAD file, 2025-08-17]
bqap_bqfb_num_7 v18.step
1131.2 x 569.2 x 1062.9 mm

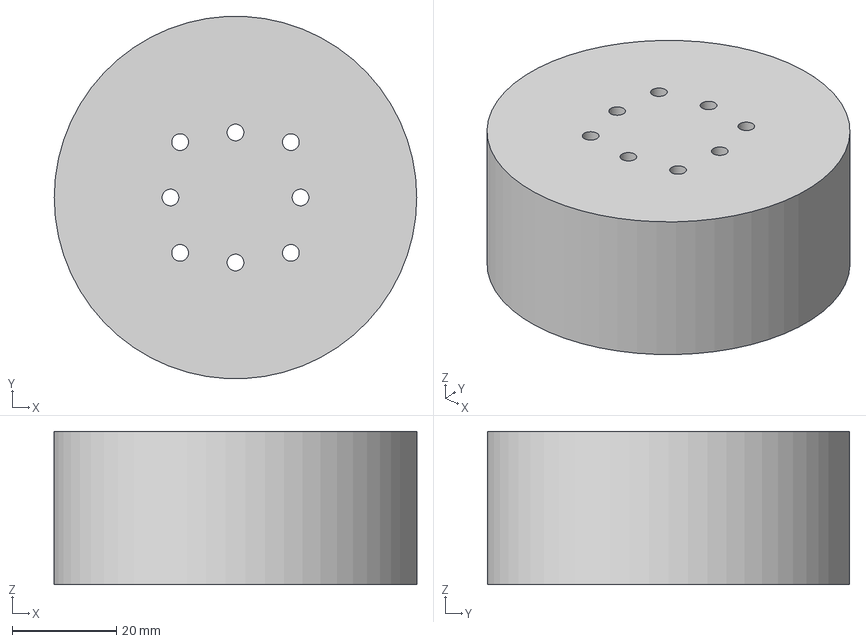
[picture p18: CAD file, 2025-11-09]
full fan parts oct 17 2025/motor dummy.step
69.4 x 69.3 x 29.3 mm

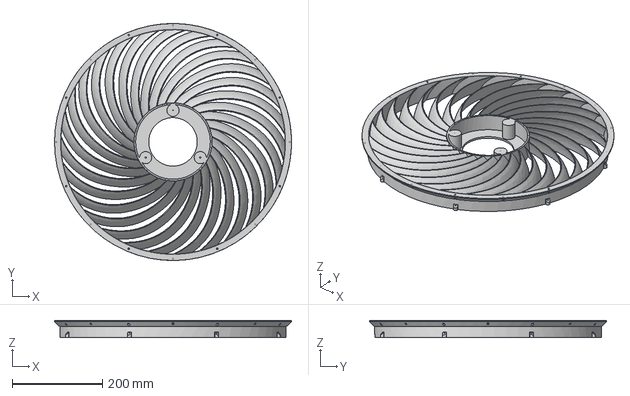
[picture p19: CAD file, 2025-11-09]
newerfanparts aug192025/secondary_thickened_16holes_errors_fixed.step
526.0 x 526.0 x 37.8 mm
bqap_bqfb_num_10 (v4~recovered)
SL57STH76-2804A - NEMA 23 stepper motor

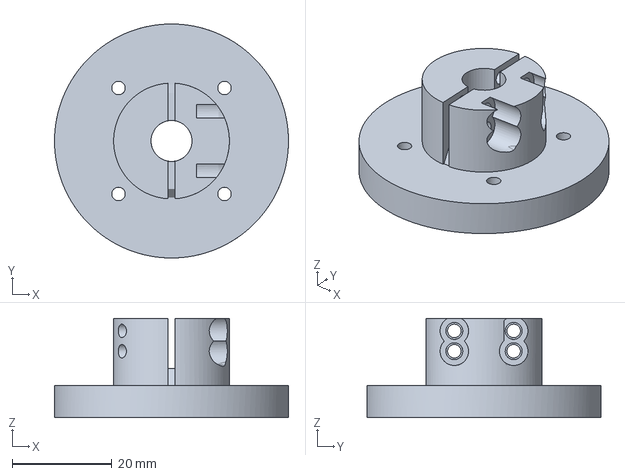
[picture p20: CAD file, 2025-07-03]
small board anemometer surface mount thermistors/anemometer_mount1.3mf
46.8 x 46.8 x 19.8 mm

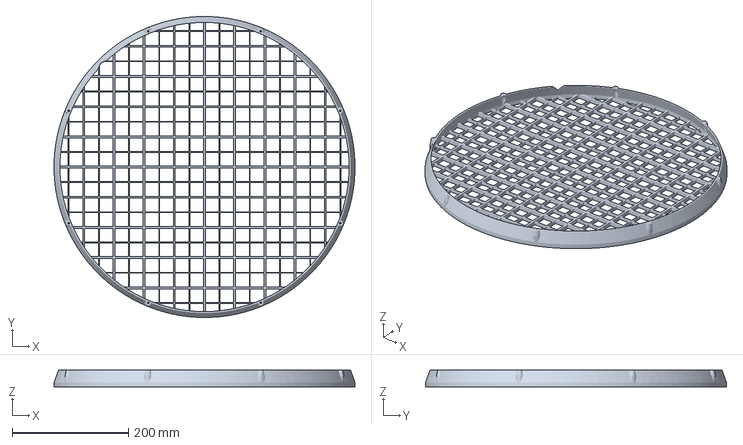
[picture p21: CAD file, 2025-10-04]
3mf/grillemoredense.3mf
518.4 x 518.4 x 29.0 mm

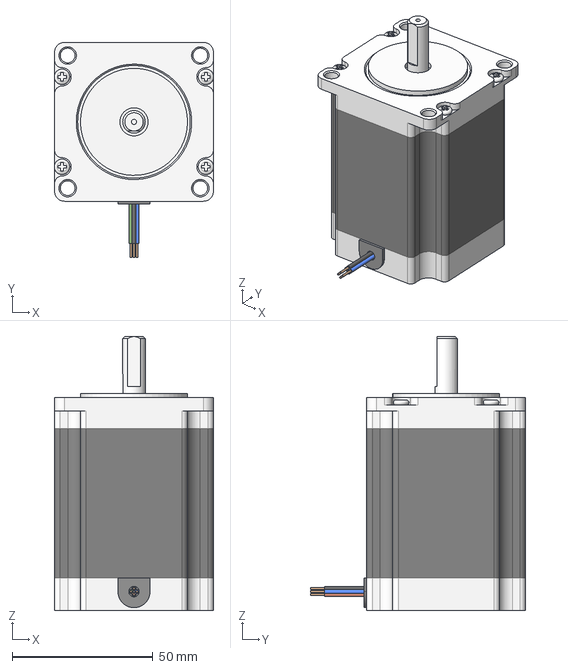
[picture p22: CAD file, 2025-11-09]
full fan parts oct 17 2025/NEMA 23 stepper motor v1.step
56.6 x 76.4 x 97.3 mm

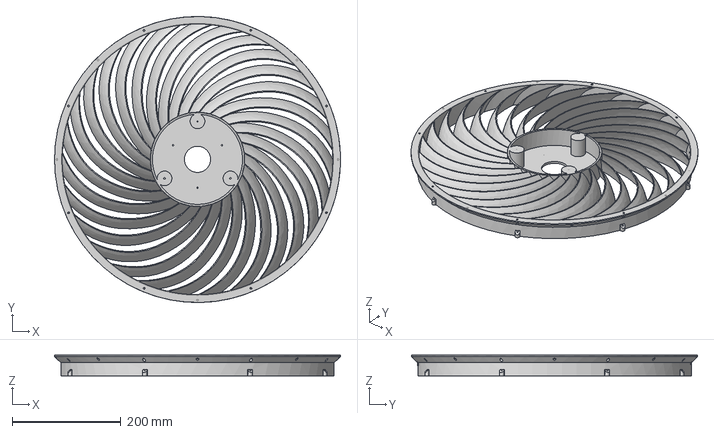
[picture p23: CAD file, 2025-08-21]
newerfanparts aug192025/secondary_thickened_16holes_combinedfromstep v2.step
526.0 x 526.0 x 38.0 mm

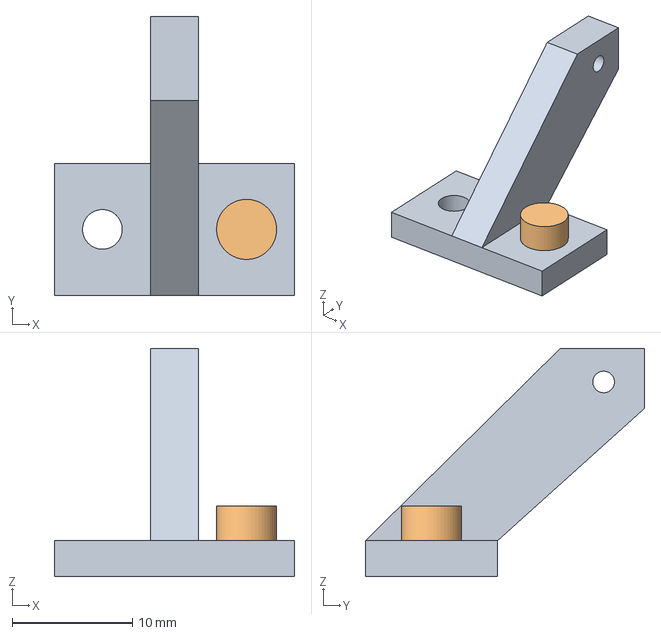
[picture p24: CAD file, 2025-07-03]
small board anemometer surface mount thermistors/anemometer mount v1.step
20.0 x 23.2 x 19.0 mm

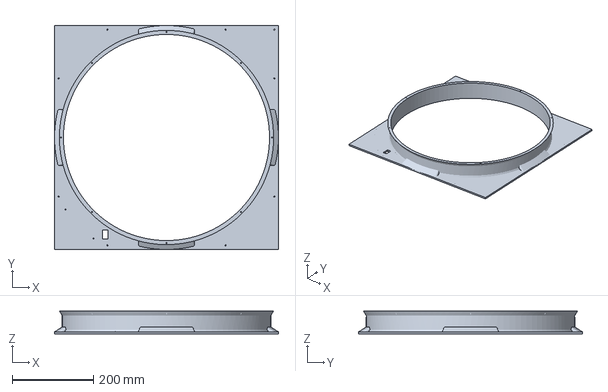
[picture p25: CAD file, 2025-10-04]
3mf/trimmedframe.3mf
550.0 x 550.0 x 56.0 mm

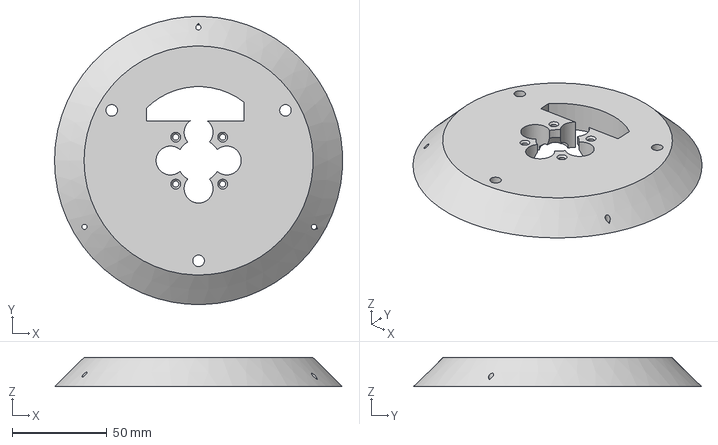
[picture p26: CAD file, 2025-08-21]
newerfanparts aug192025/motormount_au18_2025.step
152.2 x 152.2 x 15.3 mm

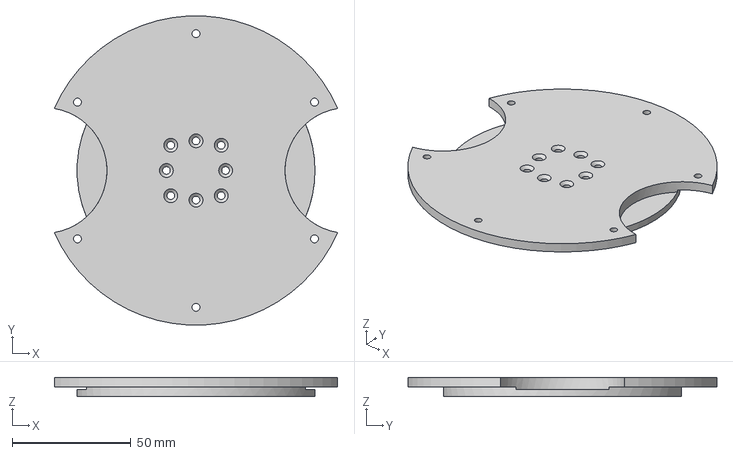
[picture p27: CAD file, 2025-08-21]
newerfanparts aug192025/asa_center_aug19_2025.step
119.1 x 129.8 x 8.00 mm

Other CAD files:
thicker fan blades and bqap/primary thickerbladesfrom num10file_backup.step
thicker fan blades and bqap/secondary_thickened_backup.step
full fan parts oct 17 2025/secondary_thickened_16holes_combinedfromstep (v2~recovered).step
3mf/v16p_thickerwalls.3mf
full fan parts oct 17 2025/thickerblades_holeforasamount.step
3mf/asa center.3mf
bqap_bqfb_num_7 v18.f3d
full fan parts oct 17 2025/anemometer mount.step
full fan parts oct 17 2025/asa_center.step
full fan parts oct 17 2025/electronics box bottom.step
full fan parts oct 17 2025/electronics box lid.step
full fan parts oct 17 2025/frame_oct17_2025.step
full fan parts oct 17 2025/grillemoredense.step
full fan parts oct 17 2025/motor mount bldc.step
newerfanparts aug192025/frame only.step
newerfanparts aug192025/grille only.step
newerfanparts aug192025/primary_thicker_blades.step
old stuff/bqap_bqfb_num_7 v18.f3d
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

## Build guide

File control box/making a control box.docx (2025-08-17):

The control box allows the BQAP to be controlled and monitored over MQTT (the protocol which the service io.adafruit uses, that is a good server to use).

It has a thing called the watchdog in it. Beware this makes connecting over the repl a bit more complicated, you have to connect before the 5 seconds are up after first boot.

You need to get an api key from io.adafruit or similar, and a username.

You need the ssid and password, put it in the persistent_vars.json file, you can edit it with any text editor. The file is machine readable, don’t mess it up, only change what’s inside the quotes.

The electrical schematic I’ll draw and get up in a minute. It’s very simple but it helps to know which pins are which.

The control box is currently powered with 5 volts from the b-g431-esc1 board. It has a regulator output for this purpose, this is common on moto drivers.

It is not particularly well tested yet but I did take it for a spin and poke and leave it running, changed everything I could think of and things seem to work without problems now.

I recommend screw terminal connectors for the wires at least, pluggable 3.81mm screw terminal connectors are good.

The cad files for the control box are in the main BQAP file, the geometry is in the main file there located in the right place. I will export stl files another time, perhaps, there is the step file there if you can’t access the fusion file.

Make sure you don’t forget the diode on the power input. That could lead to issues that could damage the usb port of a pc. Usb ports are supposed to be able to handle that kind of thing without the damage propagating to the rest of the computer, but they don’t always do that.

**important: upon first boot, if the persistent_vars.json file is not present on the pico, it is created with the defaults in the program.

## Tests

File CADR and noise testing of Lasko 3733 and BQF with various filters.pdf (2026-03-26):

# technical notes

- Data format. It is a json file which is a list of lists, in python: ['mass pm 1.0', 'mass pm 2.5', 'mass pm 4.0', 'mass pm 10',
'number pm 0.5', 'number pm 1.0', 'number pm 2.5', 'number pm 4.0',
'number pm 10', 'typical size']
- All tests are done with the filter appliance in the middle of the room, unless otherwise stated (just one in the beginning was done on a table at the end of the room to see what effect moving the machine might have)
- I acknowledge the possibility of bias, mostly unconscious, however someone has to actually do the measurements and no one else seems to be doing any, or has measured the lasko fan at lower speeds/noise levels. I offer to mail the equipment to an academic in the field who would like to do similar testing, or someone else the community could trust more.
- Ideally someone in montreal so the filters fans and everything can be sent.
- It’s Important to note that while the BQF may be considered equivalent to X many fans, that does not mean that subbing it in place of 1 fan with only 1 filter set will give X times the cadr. Consider pictures of pressure flow curves for fan and filters. Where they intersect does not increase by X times just because you have more fans, or you multiply the y axis by A to indicate increased flow at any given pressure of the fan combination (2x for instance). However, if you balance the fans out with more filters, *or filters of lower resistance/larger media area* then you can realize the potential fully.
- I acknowledge that the best thing would be curves, lots of curves, but that’s too much data to collect without more automation. So we just focus on the most relevant operating points, filter configurations etc.
- Spreadsheet with charts, same data (copied from this doc), some calculations, some info on cost etc.:
https://docs.google.com/spreadsheets/d/1gbOp7BphLow2iQUmZIKjc041NLPL7MhYoHT93j9MLzs/edit?usp=sharing (https://docs.google.com/spreadsheets/d/1gbOp7BphLow2iQUmZIKjc041NLPL7MhYoHT93j9MLzs/edit?usp=sharing)
- Github with data files and all micropython and python programs: https://github.com/adouglas89/Big-quiet-air-purifier/
- The particle sensor used was an SPS30 made by sensiron. The wiring diagram can be inferred from the micropython program, don’t forget the pullup resistors for I2C You need the right connector for it too, see it’s datasheet.
- The data is saved to an sd card, adapter module from adafruit, it has to be in smaller files rather than one big one due to ram limitations of the pico, then they are combined on the PC using a python program that is included in the github.

# test protocol

initialization:
- Put mask on

Repeat for each test:
- Assemble system, set up instruments if haven’t
- Get mixing fans running and in place
- Windows shut
- Everything sealed.
- Aerosol generator in place.
- Test machine in place.
- Get machine running with desired settings i.e. rpm. Measuring noise has to be done after or before the test, the mixing fans complicate things too much.
- Thonny open with programs, recording and non recording pm sensor programs
- Pico connected
- Sd card in logging sensor device.
- Get mask on
- Start aerosol release
- Name the folder in the python program
- Start pm sensor with non-logging program
- When it has reached about 100 (for the difference between pm1 and pm4, that is the contaminant we are measuring unless otherwise stated), halt aerosol production
- stop non logging program and start the logging program
- Start timer for 5 minutes, this is for the control test to measure background cadr of the room.
- Wait 5 minutes for control test to complete (diagnostic output in thonny will say >300000 msec since start, the alarm is just a reminder)
- After 5 minutes have elapsed since recording has started, turn on machine by plugging in power, do not adjust it in any way.
- Record
- rpm of fan
- Pressure when relevant, can be measured later with fan rpm as a reference point, for a given pair of fan/filter.
- airflow velocity at relevant point using thermanemometer, whatever it says, adjust for calibration matrix later - minimal use during test. because the mixing fans cause stray currents. Can measure it another time at the same rpm etc when measuring noise.
- We cannot measure noise at this point because the mixing fans produce too much background noise.
- Set timer for 6 minutes if expecting more than 500 cfm, 10 if less.
- Wait for timer to sound indicating test is complete
- Stop the program on the pico
- If desired, turn mixing fans off and log noise and velocity, also pressure, and velocity
- Turn the air purifier off

- Transfer data to pc using sd card, a working folder and also into a backup folder for all raw data so it never gets lost
- Copy analysis program into the working folder for the data
- Run the program to check things make sense, that test was valid. Don’t do a bunch of tests without checking everything is right/working.
- Adjust the test point times using a straight edge of a piece of paper to find the lines of best fit for the data on the log-linear plot. Changing the test point times changes the slope on the log-linear plot of the assumed line that is used to calculate cadr (the line that connects the two points).
- Make notes and record the results in this document. Spreadsheet is for later it’s hard to futz with.
- Then do next test.
Important notes:
- If the cadr is large compared to the volume of the test chamber, which is true, the result will tend to be biassed in the downwards direction due to re-inhalation of the air that just recently passed through the machine, which will reduce total particle removal when compared to performance in a large room where the air exiting the device becomes mixed with the rest of the room before re-entering the machine.
- If the sensor is close to the machine, this could bias the apparent cadr upwards as some dirty air is sort of excluded? I’m not so sure about that. Anything that reduces net particle removal would reduce apparent cadr. Re-inhalation of air that is relatively clean would do that. However I’m not so sure about this phenomena.
- Mixing fans consist of the stand fan, 1 BQF at 400 rpm and 7x P14 Max fans at 12 volts. Combined maybe 3500-4000 cfm, and they entrain air at the exit so easily 6000 cfm total air motion in the room cross section.
- The room size is:2544 cubic feet (8.8333 *12*24). There is some stuff in the room, which consumes some volume. There are no closed closets etc.

# test notes/data

Folder name: Bqap_10x_dafco_350_rpm_on_table_coscoveron:
Rpm 350 even though it says full power must have swapped the driver out at some point in the past for the lower voltage one.
Correct it later
control cadr: 223.10989679478965
test cadr before subtracting control: 976.2692585223523
apparent machine cadr: 753.1593617275627

Folder name: Bqap_10x_dafco_350_rpm_middle_of_room_coscoveron:
With the bqap in the middle of the room, or more like the western third
Mainly to compare with previous test which was same machine on a table ad the end of the room, to determine what impact the location of the machine has on measured cadr.
Rpm is only 350 fuck why? I must have swapped out the driver with the lower voltage one. Well it’s fine for this purpose
Air velocity during test at filter face : 0.33
control cadr: 63.304108878017274
test cadr before subtracting control: 874.9673265882021
apparent machine cadr: 811.6632177101849
Conclusion: the location of the machine relative to sensor and room mixing has a small impact on detected cadr. Also the background cadr varies considerably, probably due to wind.

Folder name: Bqap_10x_dafco_350_rpm_middle_of_room_NOcover:
Had to change folder name after test, forgot to set it before test.
Velocity: 0.38
control cadr: 138.51764308920082
test cadr before subtracting control: 998.4713067795774
apparent machine cadr: 859.9536636903765
Conclusion: the cover does have some impact on cadr but it’s pretty small.

bqap_10x_dafco_full_power_middle_of_room_NOcoscoveron_401rpm Bug in control box discovered, not actually run at 401 rpm but rather 350 control cadr: 193.57875539228505
test cadr before subtracting control: 945.7406700861397
apparent machine cadr: 752.1619146938547

What the fuck? The flow is clearly higher, and yet the cadr is lower? Unless the wind is fucking things up maybe, increasing control cadr, but even that does not really explain it as the figures before subtracting cadr are there. Fuck what the fuck? Obviously higher rpm must cause higher airflow and therefore higher cadr, not less. Leak in the machine? No. I did have to move it to reprogram the driver so it was capable of 400 rpm. Just try again and see what happens, if it’s the wind it will be different.

Edit: the machine boots at 400 rpm but the control box has a voltage limit that I put in back when the fan needed it, which it no longer does. When the control box kicks in it reduces the rpm to 350. So a mino r bug in the mahcine this explains the previous low rpm as well.

bqap_10x_dafco_full_power_middle_of_room_NOcoscoveron_401rpm_try2:
Failed first try, for some reason the machine reverted to 350 rpm! A minor bug in the control box. I unplugged the control box. The driver defaults to full power 400 rpm without it.
This may explain the previous baffling results.

There is duplicate data from a previous failed test in the end of the file, that is why there are two sets towards the end. I simply changed the test point 2 to avoid that region.

In the future always make a new name for the folder, do not simply restart recording, to avoid this.
control cadr: 159.06062381897192
test cadr before subtracting control: 1185.2649781347084
apparent machine cadr: 1026.2043543157365
Pressure: 7.1 pascals

bqf_4x4x20x25_3Mfiltrete_full_power_middle_of_room_NOcoscover_408rpm:
The rpm was slightly higher due to the full power resistance to airflow being lower. The drive voltage, driver and fan are the same. This would have a very small but minimal effect on noise and should be measured. By turning th emixif fans off after the test is over and measuring it.

Noise measured with mixing fans off, at 1 meter to the side of the unit:
Background meter reading:36
Meter with machine on at 408 rpm:42.5
Anmalously low, this may be because the noise meter is on the nearby bed, try holding it in the air.
Reading with machine on and noise meter in my hand at 1 meter to the side: 43.9.
Background with noise meter in my hand in same location and machine off:34.6

control cadr: 140.76931370562883
test cadr before subtracting control: 1303.6194328303734
apparent machine cadr: 1162.8501191247447
Pressure: 10.8 pascals
Testo anemometer reading taken after turning mixing fans off to prevent stray motion: 0.89m/s Discussion:
This is not much higher than the 300 rpm point according to the below, which is baffling. The data looks fine. I have no explanation really.
shitI forgot to cover the hole for the anemometer connector.

bqf_4x4x20x25_3Mfiltrete_full_power_middle_of_room_NOcoscover_300rpm:

“Full power but 300 rpm?” mistake in the naming but the test is valid. There are many more this error propagated fuck well teh data is fine and the notes are correct.
control cadr: 89.35892141208713
test cadr before subtracting control: 1154.6960570354522
apparent machine cadr: 1065.3371356233652 -> this is an outlier, exclude it from later analysis, we don’t know what happened here but this does not appear to be right. Pressure:5.8 pascals
Velocity Testo anemometer reading taken after turning mixing fans off to prevent stray motion: 0.61 m/s
REDO this test. I did, below, like 7 times as I was testing the test method at the same time to determine standard deviation

bqap_10x_dafco_NOcoscoveron_300rpm:
Pressure: 4.315 pascals
Noise with mixing fans off:39.5. The motor hum seems to have returned fuck.
Background noise:36.5
How can the pressure be lower and yet the cadr is actually lower than with the 3m 4 inch filters? Efficiency of the filters maybe?
control cadr: 94.93992867312035
test cadr before subtracting control: 745.8233692991365
apparent machine cadr: 650.8834406260162
Velocity: 0.3 m/s
Crap kind of low, lower than I thought oh well. The efficiency must go down with face velocity in some regions. With 1110 cfm flow measured previously, and 650 cfm cadr yeah that’s pretty low efficiency, not up to the merv 13 spec for 1-4 micron particles.

I forgot to turn one of the mixing fans was not turned on. It’s the smaller of the two, still a valid measure probably. This probably biassed the test downwards slightly though.

# Tests to determine standard deviation of test method due to random noise:

bqf_4x4x20x25_3Mfiltrete_full_power_on_bed_300rpm:
RPM:300
control cadr: 94.30643186951924
test cadr before subtracting control: 872.7045766136703
apparent machine cadr: 778.3981447441511

bqf_4x4x20x25_3Mfiltrete_full_power_on_floor_mid_room_300rpm-2: control cadr: 94.14786451959515 test cadr before subtracting control: 943.2026362200835
apparent machine cadr: 849.0547717004883
The time of the data points had to be adjusted for better fit to avoid blips. Obviously this is a considerable part of the noise in this kind of data. I’m basically eyeballiing a line of best fit, which is reasonable for a straight line. Might want to reprocess the data another day to use more sophisticated noise smoothing.

bqf_4x4x20x25_3Mfiltrete_full_power_on_floor_mid_room_300rpm-4:
Try 3 got messed up so we are skipping to number 4.
control cadr: 79.47466265161654
test cadr before subtracting control: 929.4653973447286
apparent machine cadr: 849.990734693112

bqf_4x4x20x25_3Mfiltrete_full_power_on_floor_mid_room_300rpm-5: control cadr: 135.15228888026897
test cadr before subtracting control: 1008.7350574415418
apparent machine cadr: 873.5827685612728

bqf_4x4x20x25_3Mfiltrete_full_power_on_floor_mid_room_300rpm-6: control cadr: 98.43813748582674
test cadr before subtracting control: 978.479831279529
apparent machine cadr: 880.0416937937023

bqf_4x4x20x25_3Mfiltrete_full_power_on_floor_mid_room_300rpm-7: control cadr: 84.31694319124526
test cadr before subtracting control: 949.0031457062802
apparent machine cadr: 864.6862025150349

Again it’s important to note I am eyeballing the line of best fit. I adjust the data point sample time slightly to get the line that they lie upon to be parallel to the eyeballed line of best fit. The exact points in time that are used are in the program, which is included with each data folder and are displayed graphically when the program is run.

bqf_4x4x20x25_3Mfiltrete_full_power_on_floor_mid_room_300rpm-8:
control cadr: 97.76200437125222
test cadr before subtracting control: 913.6108220252987
apparent machine cadr: 815.8488176540465

bqf_4x1inx20x25in_filtrete3m_300rpm:
control cadr: 175.2484430296277
test cadr before subtracting control: 964.0109847288843 apparent machine cadr: 788.7625416992566

Ok very high. Repeat this test later to be sure perhaps. However given the much higher pleating density maybe it’s to be expected. The four inch filters have only 17 pleats. The 1 inch filters have 64 pleats. If it’s the same filter media.

Bqf_4x1inx20x25in_filtrete3m_400rpm-2:
Pressure: 9.55 Pa
Airflow Velocity (middle of west facing filter while mixing fans are turned off, after the test.):0.72 control cadr: 233.00879907416245
test cadr before subtracting control: 1162.5344705545413
apparent machine cadr: 929.5256714803788

The (name)-1 test got borked, ran the wrong program for just a second when I meant to run the non logging program, which corrupted the data in the folder with that name, so that test was discarded.

The pressure indicates the flow is actually higher than it is for the 4 inch thick filters at this RPM. Lower pressure means higher flow is occurring through the fan at a given rpm.

Same filter and fan config but with the cover on, just a quick test to see what difference the cover makes, same 400 rpm:
velocity:0.6 m/s
pressure:10.55 Pa
So it does hit the flow but not that much.

Bqap_mpr1900_3mfiltrete_10x_1x20x25_400rpm-3: First two got spoiled.
control cadr: 151.60479612415796
test cadr before subtracting control: 1097.5774497156958
apparent machine cadr: 945.9726535915379
pressure:7.15.
How can the pressure be lower, indicating higher flow, than the 4x box, same type of filters, yet nearly the same cadr?
Lower cadr than the dafco filters at same fan rpm, same fan???

Bqap_mpr1900_3mfiltrete_10x_1x20x25_300rpm-1:
Pressure: 4.35
control cadr: 188.79317744421604
test cadr before subtracting control: 810.7693687459242
apparent machine cadr: 621.9761913017082
Velocity: 0.35
Again, lower cadr than the same filters in 4x box form. I ran the test for 9 minutes this time to get more data and try to be sure. I have no explanation for this phenomena except maybe how air is moving around the intake of the fan is affecting things adversely. Or maybe lower face velocity is actually reducing efficiency.edit: it appears to be the low face velocity

Also notice the velocity is unusually low compared with the pressure when compared with the 4x box, indicating some constriction due to the internal geometry.

Bqf_merv13dafco_4x_1x20x25_300rpm-1:
control cadr: 165.02405213448955
test cadr before subtracting control: 647.8531747940609 apparent machine cadr: 482.82912265957134 Pressure:7.35 Pa
Voltage:15.8 V(lab supply
Current: 0.78 A
Velocity: 0.4 m/s
Commentary: With the 10x dafco the cadr was nearly the same as using filtrete filters. With the 4x box the filtrete works much better. Oh well. That’s not a surprise, the 3m ones are usually better.

Bqf_merv13dafco_4x_1x20x25_400rpm-1:
Pressure:11.35 Pa
Voltage:23.3 V lab power supply (the cheap one reads slightly low) Current:1.43
Rpm:400
Velocity:0.6 m/s
control cadr: 240.85605929161062
test cadr before subtracting control: 915.5554454049894
apparent machine cadr: 674.6993861133788
Why is the control cadr so high?? There is no wind or anything. It varies considerably.

Lasko_3733_dafco_4x_1x20x25_merv13_525rpm:
Noise reading of meter: 43.9dBa
Background:37 dBa
Voltage AC RMS: 100
Pressure: 3.87
Rpm: 525 rpm
Speed 1
control cadr: 161.58347312541676
test cadr before subtracting control: 460.1106285595063 apparent machine cadr: 298.52715543408954

Lasko_3733_dafco_4x_1x20x25_merv13_rpm_366rpm: Noise reading: 38.5
Background noise: 34.8
Voltage rms ac: 74
Rpm: 366

Pressure:2.2 Pa
Note: the hum of the motor seems to be making most of the noise control cadr: 206.9214906204895
test cadr before subtracting control: 263.69576733461946
apparent machine cadr: 56.77427671412997
Note: remember the efficiency of the filters appears to go down as the velocity goes down. Secondly this is approaching the noise floor, so this test shows only that the value is quite low, exactly what it is is relatively uncertain. The CADR seems disproportionately low compared with the pressure. Maybe run the test again
This one’s an outlier, not clear what happened. Probably affected by wind during control period.

Lasko_3733_dafco_4x_1x20x25_merv13_rpm_382rpm:
Voltage: 78
Noise reading
Noise background:
Rpm 382
Pressure: not taken.
control cadr: 133.1394542237845
test cadr before subtracting control: 356.6302371763355
apparent machine cadr: 223.49078295255103

Note: I suspended testing when there was relatively much wind outside, and used the weather forecast to help predict calmer periods.

This one is useless the rpm is too low/below the noise value goal for some reason.

Lasko_3733_dafco_4x_1x20x25_merv13_rpm_447rpm:

Measured noise: 39.7
Background noise: 36.6
Rpm: 447
Voltage AC RMS: 92
control cadr: 176.75933574167627
test cadr before subtracting control: 441.90770696928706 apparent machine cadr: 265.1483712276108

Lasko_3733_filtrete_4x_1x20x25_mpr1900_449rpm: Measured noise: 39.7
Background noise: 36.6
Rpm 449
Voltage ac rms: 86 control cadr: 156.22107270174533
test cadr before subtracting control: 458.13643990418655
apparent machine cadr: 301.9153672024412

Lasko_3733_filtrete_4x_1x20x25_mpr1900_bqAP_frame_plus20x20mpr1900onbottom_45 0rpm:
control cadr: 141.78973915987666
test cadr before subtracting control: 418.02709281943106
apparent machine cadr: 276.2373536595544
Same rpm same noise level presumably. How can it be a lower cadr when the bottom filter is added? A combination of lower filter efficiency due to lower velocity and error in the measurement perhaps. It would not be expected to make a big difference anyway.

bqf_filtrete_4x_1x20x25_mpr1900_bqAP_frame_plus20x20mpr1900onbottom_400rpm: control cadr: 156.42918785441245
test cadr before subtracting control: 1192.1321127985902
apparent machine cadr: 1035.7029249441778
It sounds so much better than the lasko, no motor hum.

bqf_filtrete_4x_1x20x25_mpr1900_bqAP_frame_plus20x20mpr1900onbottom_400rpm_co scoveron:
control cadr: 227.92273236769734
test cadr before subtracting control: 1084.915838632181
apparent machine cadr: 856.9931062644837
Hm so the cosmetic cover does have a significant impact unfortunately. More so than it does with the vvv option.

Lasko_3733_filtrete_4x_1x20x25_mpr1900_speed1:
Pressure: ?
Voltage: 120
Rpm:665
Pressure:4.37 Pa
Measured noise: 48.9 spl 1 meter from the edge of the machine. 1 meter from center:49.5. Those measurements were made with the noise meter above the bed by 1 meter. If I measure on the other side of the machine, where there are hard background surfaces, it’s 50.8 dBa. Clearly nearby objects have an impact.
Background noise: 36.7
control cadr: 186.2548936006141
test cadr before subtracting control: 618.0370861405319
apparent machine cadr: 431.7821925399178

bqf_4x1x20x30_mpr220_3m_1x1x20x20_mpr1900_3m_400RPM: control cadr: 101.54635000992407
test cadr before subtracting control: 962.4905801725301 apparent machine cadr: 860.9442301626061

Voltage: 24.3
Current: 1.6
Rpm: 400
Ok so that sucks, don’t do that. Crap I had high hopes for that one. The legs may have a minor effect, they were 6 cm long

Lasko fan speed 3 4x1x20x25 filtrete mpr 1900 plus 1x20x20 mpr1900 filtrete on bottom (5 filter config):
Pressure:5.95 pascals.
Noise: 60.8 . background nearly irrelevant
Background noise:38 dBa (window open)

I guess I never got around to performing this test

BQF_6x_dafco_1x20x25_merv_13_300rpm:
300 rpm
control cadr: 139.72823076953804
test cadr before subtracting control: 705.5997930961275
apparent machine cadr: 565.8715623265895
This is with the single v in the middle, wooden frame, with the thicker blades fan, the thicker blades shouldn’t make any difference.

BQF_6x_dafco_1x20x25_merv_13_400rpm:
400 rpm
control cadr: 58.96686540607321
test cadr before subtracting control: 955.0802848044497
apparent machine cadr: 896.1134193983764
Let’s redo this test, the control cadr seems anomalously low, I forgot to turn on one of the mixing fans during the control phase. If leaving the fan off reduces background cadr, then the reduction x2 would be the error created. Because it is subtracted from the background cadr and then added to the test cadr.

BQF_6x_dafco_1x20x25_merv_13_400rpm-2:
control cadr: 85.9590369731942
test cadr before subtracting control: 899.5338379673203
apparent machine cadr: 813.5748009941261
Note: there was a mistake with this test, I forgot to tape up some gaps in the machine, this would have biassed the result downwards. Since it is high, the filters are cheap and it might b ethe best combo, it would be a good idea to redo this test. Two in a v in the middle and four on the sides. That would eliminate the need for the 20 by 20 and also to use filtrete filters, if it goes well.

Bqf_4x1x20x25_dafco_merv-13_1x20x20_mpr1900_filtrete_nocover_400_rpm wanted
Bqf_4x1x20x25_dafco_merv-13_1x20x20_mpr1900_filtrete_nocover_300_rpm wanted
Bqf_4x1x20x25_dafco_merv-13_1x20x20_mpr1900_filtrete_withcoscover_400_rpm Wanted
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

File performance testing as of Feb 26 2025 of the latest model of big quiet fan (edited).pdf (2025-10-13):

## The performance as of Feb 26 2025 of the latest model of big quiet fan (funded by grant A42)

Note Sept 22 2024: This document describes a slightly inferior older prototype. The latest prototype gets the same pressure/flow relationship, but with lower noise due to the use of a polymer with better damping. Noise is only about 42 dBa now.

This document describes the performance of the Big Quiet Fan, latest model as of Feb 25, the test procedures/data reliability, and comparisons to the next best fan for flow to noise ratio in the context of building air filter boxes, which is apparently the Arctic P14 (the SickelFlow is also pretty good but very similar so I focussed on the P14 since it’s commonly used and is the next best fan discussed in the grant application). The Big Quiet Fan revision under test is the Version 11 primary version 10 secondary, version 6 frame, for reference.

It’s important to note that work continues, to evolve the fan in several ways, by improving the motor driver to eliminate or reduce motor hum, and also to improve the blade design (probably only minor progress will be made on the blade design from this point on). The motor driver will be replaced with the open source one I am working on with the SimpleFOC community (especially Sequoia) at some point.

My old thermanemometer fried itself, so I got a new one and validated it using a rotating arm apparatus for the measurements in this document (pictures and brief description below). This one works better at low velocity, and it’s accuracy is now known and can be corrected, even, using the table built during the validation process.

There are four sources of data I can use:
- ATOM, the engineering firm that Air Support Project hired to do various things, including evaluate fans and filters. That data is for the old V6 fan, which has inferior performance, and also there are some problems with the acoustic data, making it unusable (it’s sound power rather than the standard sound pressure level at 1 meter, which can be converted crudely to SPL at 1 meter, but also there are considerable actual errors, as shown by my sound meter). The measurements of the flow to pressure ratio of the filters also does not match my measurements at all/cannot be replicated. This makes me trust the data very little. It was also taken at different RPM values than my standard test points, which make it hard to use precisely. I take data at 300 and 400 rpm usually, taking a range of data at a range of RPMs every time I changed something would not be practical or cost effective. For these reasons I have not used this data much, but we can use the flow/pressure values for the P14 fan at least, which I have also measured, and my measurements of those parameters are essentially in line with theirs, and also the manufacturer’s
(https://support.arctic.de/products/p14-pwm-pst/techdocs/P14%20-%20PQ%20Curve%2 0for%20CFD.XLSX) (https://support.arctic.de/products/p14-pwm-pst/techdocs/P14%20-%20PQ%20Curve%20for%20CFD.XLSX) (the manufacturer’s indicates slightly higher values, and at the same time lower rpms which would make it quieter).

- The second source is Joshua Pearce’s lab, at the University of Western Ontario, who has taken thermal data mostly but is planning to get some acoustic data soon. This is the most reliable because they are academics that are in the habit of being quite precise to protect their reputation, but does not include pressure and flow data yet, and it’s going to be a while before they get around to that. They mostly want it for a greenhouse anyway so such testing is not a priority. They have however already produced a report on some aspects of the fan, which IMO does not have much bearing here except to indicate it works ok and verify the power consumption at various RPM, but you can see it at
https://docs.google.com/document/d/1Fr6ZwluvgL4xyAOdBe_uR3tBEItB9S_Q/edit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
- The third is information on noise and subjective evaluation from HouseFresh, the organization in the UK that tests air filter appliances. I sent them a V11P/V10S fan mid january I think, shipping took a long time and they are getting around to testing soon hopefully. They have a class 2 sound meter and will build a filter box appliance of some kind and test the CADR with their usual methodology, which is unfortunately not a direct measure of absolute CADR but can be used as an apples to apples measure to compare the CADR of different appliances they have tested, they are still working on that, I have discussed this with them.
- Lastly, there is the data I have collected, which I have the most confidence in because I know exactly how it was collected, it is for the right fan and filter arrangement, it is at the right RPMs and using the same equipment and environment every time. Although done on a small budget, and I have learned the hard way that bias takes many forms, it is I think quite dependable at this point. This is because of the anemometer validation, and also the manometer, sound meter, ammeter, voltmeter (built into power supply), and tachometer are pretty solid.
- The sound meter is an IEC class 2 meter which is a regulated device used for checking noise levels in the workplace for regulatory compliance, it’s accuracy is 2-3 dB. It’s precision/repeatability is considerably higher than that though, so the measurements I have made of the ratio of the noise produced by the P14 vs BQF for instance, largely circumvent that concern. The difference between two noise sources should be reflected with a precision and accuracy considerably higher than 2-3 dB. The background noise is the main source of error, it can theoretically be subtracted from the signal, and I have tried to do this, but the process can amplify error to some moderate degree. I do not know how the manufacturing chain of this device goes or where the regulatory oversight plays in but it appears to be reliable from every angle I have been able to look at it. Checking it the way I checked the anemometer is not something I can presently see a way to do. A rotating rod of precise geometry and rotational speed could be a reliable source of noise for calibration, but that’s a pipe dream for now. I have checked it in several ways, for instance two identical noise sources is higher than one by 3 decibels, which is as expected. The noise level indicated also goes down with distance from the source as expected.

- The manometer is an SDP810-125A sensor, which I have used many times in various contexts and found remarkably reliable, and is consistent with water manometer and tilted oil manometer readings. I have a tilted oil manometer to verify things, but it’s not as reliable, repeatable or accurate as the SDP810-125A. The data sheet says the SDP810-125A is calibrated at the factory and is accurate to within 0.1 pascals even at these low pressures. Ironically, it’s actually a thermanemometer internally - pressure is inferred from the rate of flow through a small hole - but because the flow pattern etc. can be controlled inside the casing, it is consistent and reliable.
- The ammeter and volt meter are not particularly important but are built into the power supply. I have checked them incidentally many times over the years with a VOMM and it always seemed to agree.
- The tachometer is important for reliability but it’s accuracy and repeatability come directly from electronic oscillators and electronics/optical devices so it’s precision and accuracy is not something I am worried about.

Apparatus:

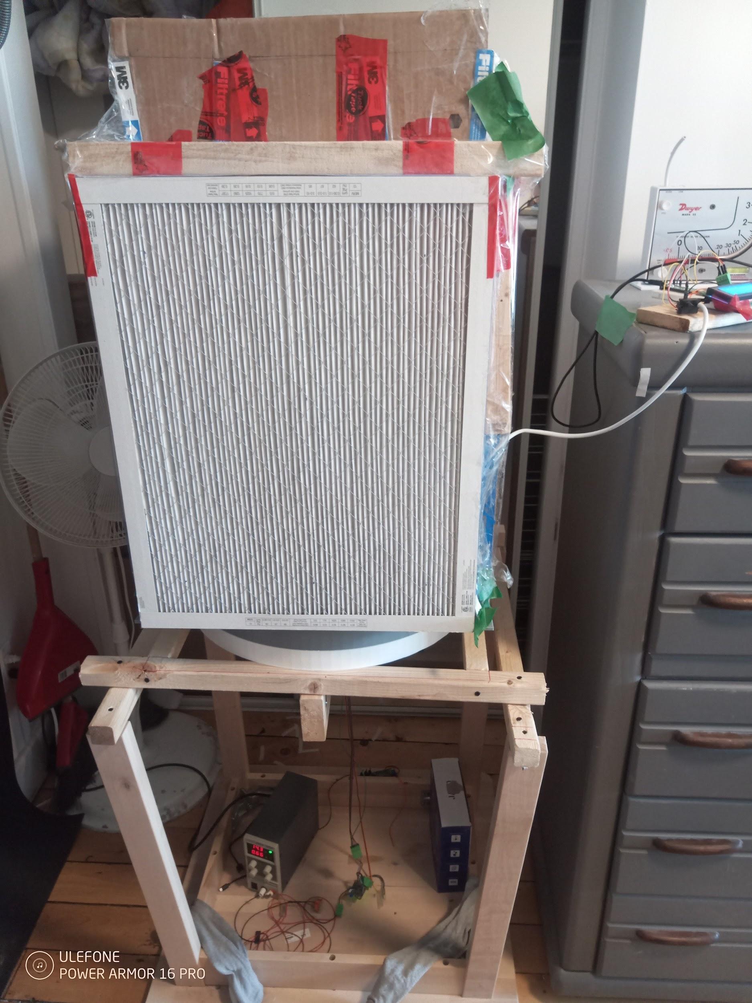
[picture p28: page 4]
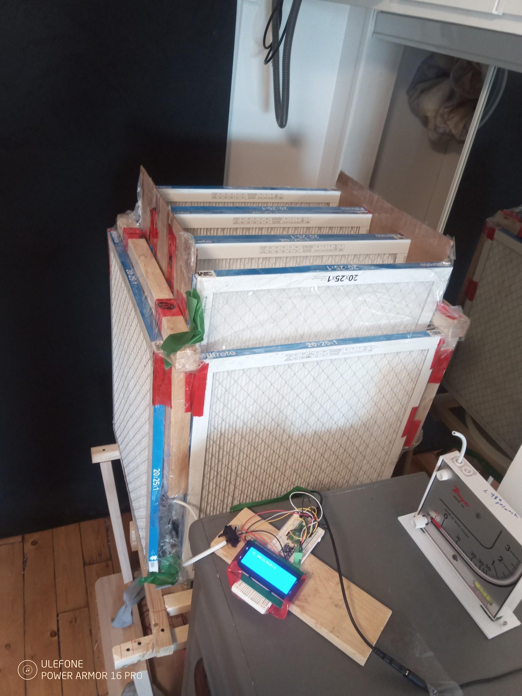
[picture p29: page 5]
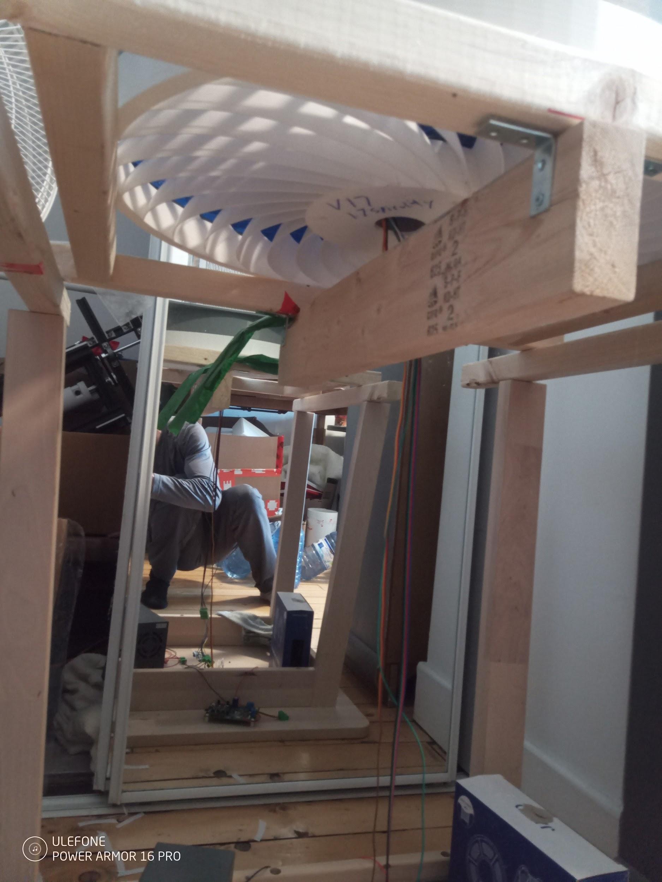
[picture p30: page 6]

The apparatus consists of the filter set, which is 10 3M Filtrete brand 20 inch by 25 inch MERV 13 filters taped into an arrangement with a “triple V” in the middle, and 4 filters around the periphery. This is meant to be close to the final filter appliance I am optimizing for. In any optimality search there has to be a certain context, end use parameters of some kind, and I have adopted a set of 10 filters, in this arrangement, as that context.

There is some space internally for air to flow at the flat sides of the V, but air is still being restricted quite significantly in many areas, which could be improved by spacing the filters further apart in the final appliance. It provides the needed functionality for testing just fine, though. For example the total flow in the top of the device is only 2.5 times the flow rate of the filters on the side, despite there being 6 filters for air to flow through the triple V. Secondly, the variation in flow velocity between the top of the side filters and the bottom of the filters is about a factor of 3. This indicates very considerable effect of aerodynamic pressure drop internal to the assembly in the different areas, which I did not expect.

Again, this internal restriction of airflow was the main source of error in early measurements and extrapolation, combined with the fact I could not just measure the airflow because my anemometer did not function at these low flow values. The new one does.

It may not be clear from the picture, but the center timber is 1.5 inches away from the fan, allowing air to flow reasonably well although I’m sure it has a small negative impact, given the high flow rates and low pressures.

The fan was powered up to 300 and then 400 RPM, and the validated thermanemometer used to measure the flow at the points indicated in the diagram in in the spreadsheet, and entered into the spreadsheet listed.

Spreadsheet of test data and computations: https://docs.google.com/spreadsheets/d/1RyS2FexTkQHimqX9ASrzR0OXF6ZEogR1g6wwQfYa-e4/edit?usp=sharing (https://docs.google.com/spreadsheets/d/1RyS2FexTkQHimqX9ASrzR0OXF6ZEogR1g6wwQfYa-e4/edit?usp=sharing)
(See the other tabs for flow rate measurements of the actual test rig)

# Conclusion of testing drawn from spreadsheet:

300 rpm: 37.5 dBa at 1 meter with filters on. 3.8 pascals, 1111 CFM.
400 rpm: 47.3 dBa at 1 meter with filters on. 5.6 pascals, 1452 CFM.
Edit march 12 2025: There should be certainty or error bars here, unfortunately they would themselves be estimates, and as you will see we can actually cancel out some of the latent error when comparing things.

Higher flow may be possible with a better filter arrangement.

Lower noise may be possible especially in the 300 rpm range with a motor that makes less noise, or modifications to the motor driver to cancel out the hum (anti-cogging), it is a considerable fraction of the noise, I don’t know exactly how much, but I can hear it. Also a spectrum analyser app indicates this to be true as well. This is in progress.

# Comparison with P14 fan:

## At 300 RPM:

At the pressure of 3.8 pascals (0.015265 inches water column), the P14 fan according to ATOM’s data( https://docs.google.com/spreadsheets/d/1a7mojU1EStVRD1M9MlaQoEpgtmqV-c7MnrezLvrI9aY/edit?usp=sharing) (https://docs.google.com/spreadsheets/d/1a7mojU1EStVRD1M9MlaQoEpgtmqV-c7MnrezLvrI9aY/edit?usp=sharing) gets about 62.5 CFM (halfway between the second and third data points).

The noise level of the P14 fan operating at 12 volts and indeed the same 1800 RPM, I measured with my sound meter is 35 decibels Sound Pressure Level at 1 meter (the ATOM data is Sound Power level, which is not the same measure, that’s why it’s different). This is done by subtracting the linearized background noise pressure level reading from the linearized noise level and then converting back to decibels (Assumed actual noise level emitted by device = 10*log10(10**(reading/10)-10**(background/10))).

I confirmed the flow rate appears to be about right using my anemometer, a 6 inch diameter pipe and a plastic adapter plate, the pieces used are shown in the pictures below. Even a pipe of this diameter causes significant pressure drop at this flow rate, about 4 pascals. This kind of phenomena is the same that led to the internal flow restriction inside the filter arrangement.

The flow rate at this pressure of the BQF is therefore 1111/62.5 = 17.78 times the flow rate of a single P14 fan. The noise level of the BQF is 2.5 decibels higher, therefore 10*2.5/10 = 1.78 times the noise level of a single P14 fan (sound pressure level is proportional to sound power emitted by a device, all else being equal). Therefore the flow to noise ratio is 9.98 times higher. Edit march 12 2025: Again, the question of error bar or uncertainty is important here, as relatively small variations in the dBa difference will affect this figure quite considerably. However, the main point is that it’s pretty good. The input figures would have to change very considerably for this to drop below 1. In my opinion it’s a very safe bet that things are quite good, when you sum it all together.

The original goal in the proposal was to get 16 times the flow of a P14 fan, at the relevant pressure, while getting the same or better flow to noise relationship as a P14 fan (1 or higher). With a ratio of 10 times higher flow to noise, I have therefore considerably exceeded the goals at this pressure and flow test point, which is the most relevant.

Again it is possible to reduce the noise of the BQF further by eliminating the motor hum.

## At 400 RPM:

The BQF gives 5.6 pascals through the filter assembly at 400 RPM. At 5.6 pascals (0.0225 inches water column), the P14 gets 57 CFM, same noise level as at 3.8 pascals.

From the data above, the BQF therefore gets 25.45 times the flow at this RPM and pressure, as a P14 fan. It gets 12.5 decibels higher noise, which is 17.78 times the noise. Therefore the ratio of flow to noise at this pressure and RPM is 1.43. Clearly an array of 25 p14 fans is not practical, so this is a considerable advance, and greatly exceeds the original proposal’s goal of 16x the flow and 1x the flow to noise ratio.

# Confirmation of noise level from UWO and HouseFresh:

This is pending.

More pictures:

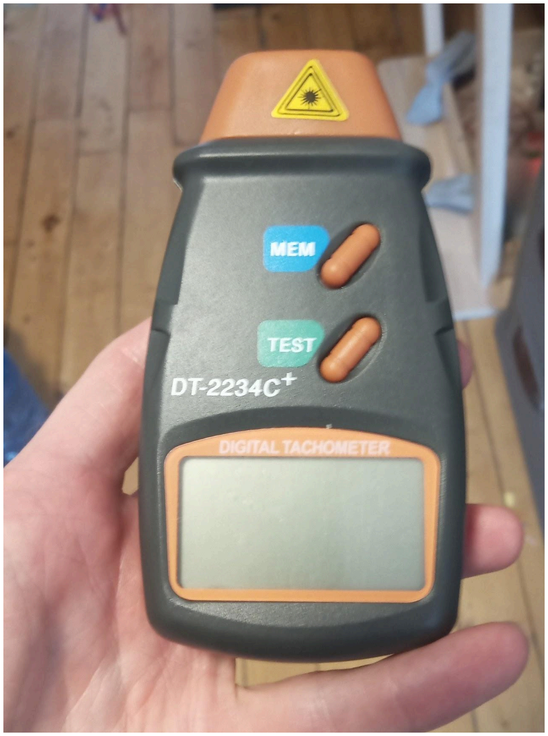
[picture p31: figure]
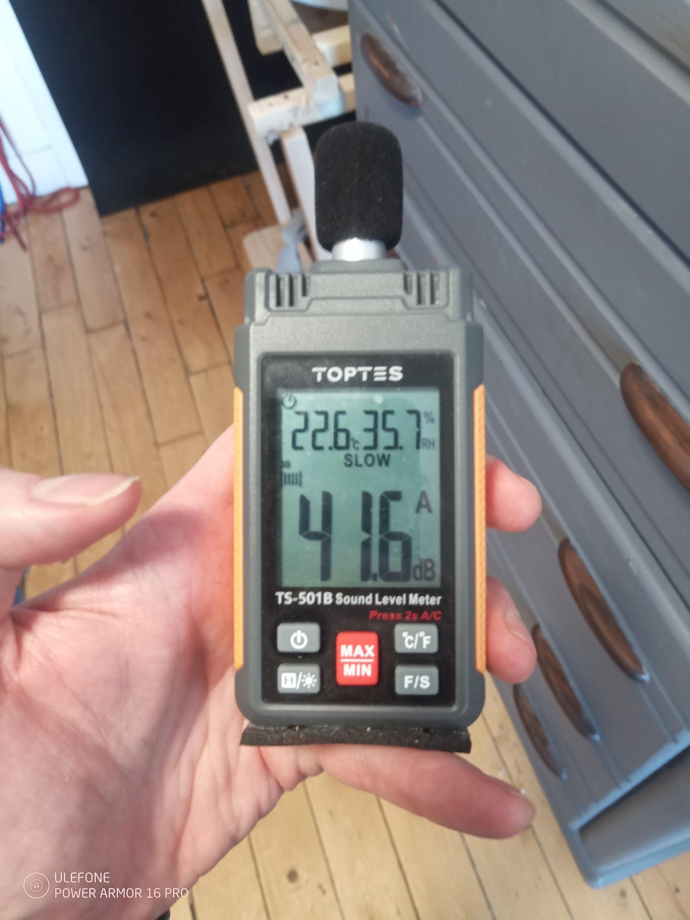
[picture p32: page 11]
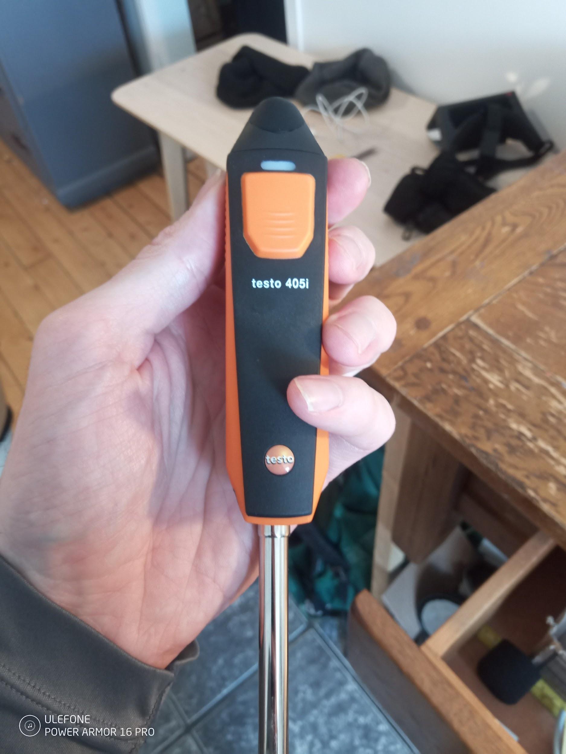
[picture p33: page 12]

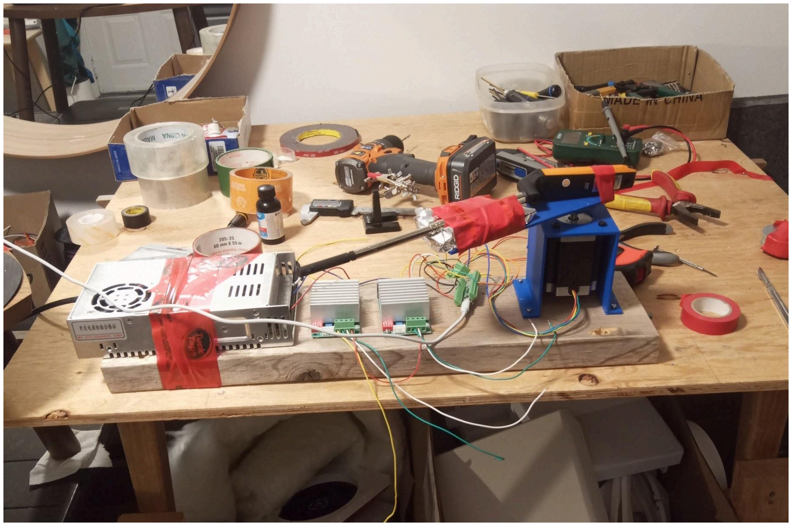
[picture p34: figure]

The anemometer test apparatus actually used a TMC2209 stepper driver to get smooth motion, the two stepper drivers in the foreground are not used. The distance between the center of rotation and the sensor of the thermanemometer is measured, and then the sensor rotated at a known speed. Data was taken and a spreadsheet constructed to ensure it was adequately reliable and allow for compensation to be done, even.

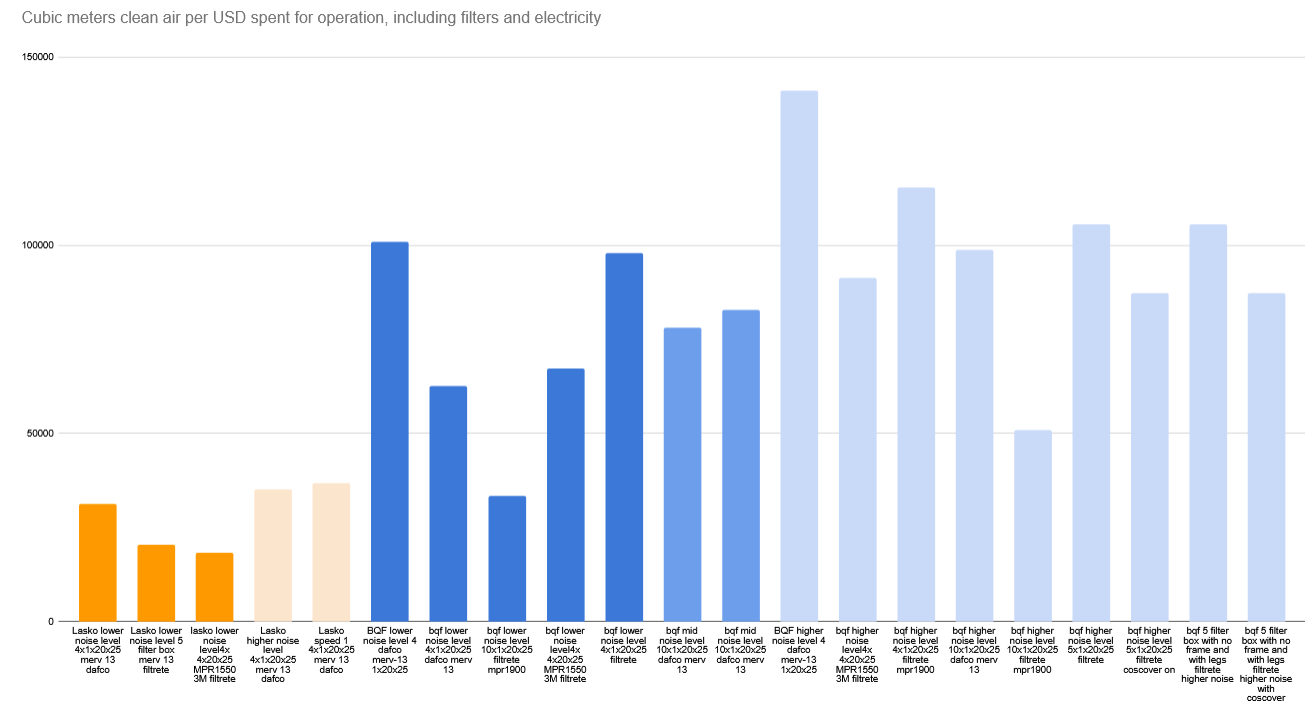
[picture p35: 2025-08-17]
cadr testing/pic of cubic meters per usd.png

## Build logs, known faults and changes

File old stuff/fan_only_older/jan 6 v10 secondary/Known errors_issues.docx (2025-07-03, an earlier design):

The V11 secondary, which is not expected to be used, has some errors, one component is not quite centered and thus the blades do not all connect to the hub nordoes the edge connect to the outer area quite right.

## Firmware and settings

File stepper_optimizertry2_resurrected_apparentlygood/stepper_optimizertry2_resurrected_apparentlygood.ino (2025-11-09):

#include <Arduino.h>
#include <SimpleFOC.h>
#include <math.h>

// ---------- USER PINS (Raspberry Pi Pico 2W) ----------
static const int PIN_PWM_AH = 4;
static const int PIN_PWM_AL = 5;
static const int PIN_PWM_BH = 6;
static const int PIN_PWM_BL = 7;
static const int En_a       = 8;
static const int En_b       = 9;
static const int POT_PIN    = 26;  // ADC0
static const int CURR_PIN   = 28;  // ADC2

// ---------- MOTOR / DRIVER ----------
StepperMotor motor = StepperMotor(50);
StepperDriver4PWM driver = StepperDriver4PWM(PIN_PWM_AH, PIN_PWM_AL, PIN_PWM_BH, PIN_PWM_BL, En_a, En_b);

// ---------- SPEED / POT ----------
volatile float RPS       = 0.0f;
volatile float RPS_accel = 0.3f;    // rps^2 
volatile float rps_max   = 7.5f;
const float    HYST_RPS  = 0.5f;    // rps hysteresis band
unsigned long  lastMicros = 0;

// ---------- CURRENT READ ----------
float read_current_units() {
  // raw ADC voltage (0..3.3 V) proportional to current; absolute amps not required for minimization
  int raw = analogRead(CURR_PIN);
  return 3.3f * (float)raw / 4095.0f;
}

// ---------- OPTIMIZER (ΔV trim around base voltage) ----------
struct MinCurrentTrimOpt {
  // Voltage bounds (motor command)
  float Vmin = 3.0f;
  float Vmax = 24.0f;

  // Trim state (what we adjust): Vcmd = clamp(Vbase + trim)
  float trim = 0.0f;

  // Step logic
  float step     = 0.10f;   // initial trim step (V)
  float step_max = 0.30f;
  float step_min = 0.02f;
  int   dir      = +1;      // +1 / -1

  // Filtering & decision
  float Ibar   = 0.0f;      // EMA of current
  float alpha  = 0.15f;     // EMA coeff (0..1)
  float Iref   = INFINITY;  // drifting reference (best so far with drift)
  float eps    = 0.02f;     // significant improvement threshold 
  float drift  = 0.003f;    // upward drift rate for Iref (keeps optimizer adaptive)

  // Timing
  uint32_t lastTickUs = 0;
  uint32_t periodUs   = 10000;  // 10 ms tick
  int      settleTicks = 8;     // ~80 ms settle after each voltage change
  int      settleLeft  = 0;

  // simple rate-limited debugging
  uint16_t printEvery = 25;
  uint16_t printCnt   = 0;

  // helpers
  inline float clampV(float v) const { return constrain(v, Vmin, Vmax); }

  static inline float ema(float prev, float sample, float a) {
    return prev + a * (sample - prev);
  }

  void init() {
    trim = 0.0f;
    step = 0.10f;
    dir  = +1;
    Ibar = 0.0f;
    Iref = INFINITY;
    settleLeft  = settleTicks;
    lastTickUs  = micros();
    printCnt    = 0;
  }

  void applyCommand(float Vbase) {
    float Vcmd = clampV(Vbase + trim);
    motor.voltage_limit = Vcmd;
  }

  void tick(float Iraw, float Vbase) {
    uint32_t now = micros();
    if (now - lastTickUs < periodUs) {
      return; // wait until next tick
    }
    lastTickUs = now;

    // Update filtered current
    Ibar = ema(Ibar, Iraw, alpha);
    if (isinf(Iref)) Iref = Ibar;            // first sample
    // Let the "best" baseline drift upward to follow changing conditions
    if (Ibar > Iref) Iref += drift * (Ibar - Iref);
    else             Iref  = Ibar;           // if we see lower current, follow it immediately

    // Settling time after a voltage change
    if (settleLeft > 0) {
      settleLeft--;
      applyCommand(Vbase);
      return;
    }

    bool improved = (Ibar + eps < Iref);

    if (improved) {
      // Accept direction; slightly grow step
      step = min(step * 1.2f, step_max);
      // Advance trim in same direction
      trim += dir * step;
      // Keep command within bounds (relative to Vbase)
      float Vcmd = clampV(Vbase + trim);
      // If clamped, flip and shrink
      if (Vcmd == Vmin || Vcmd == Vmax) {
        trim = Vcmd - Vbase;
        dir  = -dir;
        step = max(step * 0.5f, step_min);
      }
      settleLeft = settleTicks;
      Iref = Ibar; // new local best
      applyCommand(Vbase);
    } else {
      // Backtrack: flip direction & shrink step
      dir  = -dir;
      step = max(step * 0.5f, step_min);
      trim += dir * step;
      // Bound again
      float Vcmd = clampV(Vbase + trim);
      if (Vcmd == Vmin || Vcmd == Vmax) {
        trim = Vcmd - Vbase;
      }
      settleLeft = settleTicks;
      applyCommand(Vbase);
      Serial.println(motor.voltage_limit);
    }

    // (Optional) light debug printing, rate-limited
   // if (++printCnt >= printEvery) {
   //   printCnt = 0;
  //    Serial.print("Ib"); Serial.print(Ibar, 3);
  //    Serial.print(" I"); Serial.print(Iref, 3);
 //     Serial.print(" V"); Serial.print(Vbase, 3);
 //     Serial.print(" t");  Serial.print(trim, 3);
 //     Serial.print(" s");  Serial.print(step, 3);
  //    Serial.print(" d");   Serial.println(dir);
  //  }
  }
} opt;

// ---------- SETUP ----------
void setup() {
  Serial.begin(115200);
  // while (!Serial) {}

  // GPIO modes (SimpleFOC may reconfigure as needed)
  pinMode(PIN_PWM_AH, OUTPUT_12MA);
  pinMode(PIN_PWM_AL, OUTPUT_12MA);
  pinMode(PIN_PWM_BH, OUTPUT_12MA);
  pinMode(PIN_PWM_BL, OUTPUT_12MA);
  pinMode(LED_BUILTIN, OUTPUT);

  // ADC
  analogReadResolution(12);

  // Driver
  driver.voltage_power_supply = 24.0f;
  driver.voltage_limit        = 24.0f;   // driver ceiling
  driver.pwm_frequency        = 30000;   // 30 kHz PWM
  if (!driver.init()) {
    Serial.println("Driver init failed!");
    while (1) { delay(1000); }
  }
  driver.enable();

  // Motor
  motor.linkDriver(&driver);
  motor.controller         = MotionControlType::velocity_openloop;
  motor.velocity_limit     = 50.0f;           // rad/s ceiling
  motor.foc_modulation     = FOCModulationType::SinePWM;
  motor.modulation_centered = false;
  motor.init();

  opt.init();               // initialize optimizer state (after motor.init)
  lastMicros = micros();

  Serial.println("Stepper: pot-controlled RPM + online ΔV trim for min current");
}

// ---------- LOOP ----------
void loop() {
  // --- Pot to target RPS ---
  int raw = analogRead(POT_PIN);
  float norm   = (float)raw / 4095.0f;      // 0..1
  float target = norm * rps_max;            // RPS target

  // --- Time step for RPS ramp ---
  unsigned long now = micros();
  float dt = (now - lastMicros) * 1e-6f;
  lastMicros = now;

  // --- RPS ramp with hysteresis & accel limit ---
  float err = target - RPS;
  if (fabsf(err) > HYST_RPS) {
    float maxStep = RPS_accel * dt;
    if (err > 0.0f) RPS += min(err,  maxStep);
    else            RPS += max(err, -maxStep);
  }
  RPS = constrain(RPS, 0.0f, rps_max);

  // --- Base voltage from RPM (kept simple) ---
  float Vbase = (19.0f * (RPS / rps_max)) + 3.0f;   // maps 0..rps_max -> 3..16 V
  Vbase = constrain(Vbase, opt.Vmin, opt.Vmax);     // ensure within bounds

  // --- Read current & optimize trim at ~100 Hz ---
  float Iraw = read_current_units();
  opt.tick(Iraw, Vbase);    // opt writes motor.voltage_limit each decision tick

  // --- Command motor speed (rad/s) ---
  float cmd_rad_per_sec = RPS * 2.0f * PI;
  motor.move(cmd_rad_per_sec);  // one call per loop keeps things responsive

  // (Optional) You can call motor.loopFOC() here if using closed-loop in the future
  // motor.loopFOC();
}

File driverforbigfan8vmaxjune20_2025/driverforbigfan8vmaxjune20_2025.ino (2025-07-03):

 #define polepairs 11

 #include <Arduino.h>
#include <SimpleFOC.h>
#include <SimpleFOCDrivers.h>
#include <encoders/smoothing/SmoothingSensor.h>
BLDCMotor motor = BLDCMotor(polepairs);
BLDCDriver6PWM driver = BLDCDriver6PWM(A_PHASE_UH, A_PHASE_UL, A_PHASE_VH, A_PHASE_VL, A_PHASE_WH, A_PHASE_WL);
LowsideCurrentSense currentSense = LowsideCurrentSense(0.003, -64.0/7.0, A_OP1_OUT, A_OP2_OUT, A_OP3_OUT);
// hall sensor instance
HallSensor sensor = HallSensor(PB6,PB7,PB8, polepairs);
SmoothingSensor smooth(sensor, motor);

// Interrupt routine intialisation
// channel A and B callbacks
void doA(){sensor.handleA();}
void doB(){sensor.handleB();}
void doC(){sensor.handleC();}


// voltage set point variable
float target_voltage = 0;
bool voltage_override = 0;
float maybe_v = 1;
float voltage_max = 8;
float goal_v = voltage_max;
float accel = 1;// in volts per second
void SerialComm(){ 
  if (Serial.available() > 0){
  switch(Serial.peek()){
      case 'c': Serial.read(); Serial.print("c"); Serial.println(accel); break;
      case 'o': Serial.read(); Serial.print("o"); Serial.println(voltage_override); break;
      case 'v': Serial.read(); Serial.print("v"); Serial.println(motor.target); break;
      case 's': Serial.read(); Serial.print("s"); Serial.println(motor.shaftVelocity()); break;
      
      //case 'g': Serial.read(); Serial.print("g"); Serial.println(currentSense.getDCCurrent(), 5); break;
     // case 'i': Serial.read(); Serial.print("i"); Serial.println(get_mA(), 4); break;
      //case 'y': Serial.read(); Serial.print("y"); Serial.println(_readADCVoltageInline(A_POTENTIOMETER, currentSense.params)*0.305810398); break;
  case 'V': break;
  default: Serial.read(); break; //if anything we don't recognize got in the buffer, clear it out or it will mess things up.
       
  }
}
  if (Serial.available() >= 9){//if there are 9 or more characters in there
  switch(Serial.read())
  { 
  case 'V': 
    maybe_v = Serial.parseFloat(); // just in case the wrong data gets in somehow we don't want the voltage going crazy
    if (maybe_v < 0){

      maybe_v = 0;
      } 
    if (maybe_v >= voltage_max){ 
    
      maybe_v = voltage_max;
    }
    goal_v = maybe_v;
    break;
  }
  }
}
void setup() { 
  pinMode(PB4, INPUT_PULLUP);
  sensor.pullup = Pullup::USE_INTERN;
  smooth.phase_correction = -_PI_6;
  Serial.begin(115200);
  Serial.println("test serial2");
  // enable more verbose output for debugging
  // comment out if not needed
  SimpleFOCDebug::enable(&Serial);

  // initialize encoder sensor hardware
  sensor.init();
  sensor.enableInterrupts(doA, doB, doC); 
  // link the motor to the sensor
  motor.linkSensor(&smooth);

  // driver config
  // power supply voltage [V]
  driver.voltage_power_supply = 24;
  driver.init();
  // link driver
  motor.linkDriver(&driver);

  // aligning voltage
  motor.voltage_sensor_align = 1.1;
  
  // choose FOC modulation (optional)
  motor.foc_modulation = FOCModulationType::SinePWM;

  // set motion control loop to be used
  motor.controller = MotionControlType::torque;
  // initialize motor
  motor.init();
  // align sensor and start FOC
  motor.initFOC();

}


float looptime_seconds = 0;
bool underspeed_start = 0;
void loop() {
  static unsigned long underspeed_detect_start;
  static unsigned long lastTime = millis();
  unsigned long now = millis();
    unsigned long looptime_ms = now - lastTime;
  lastTime = now;
looptime_seconds = float(looptime_ms)/1000;
if (goal_v > (target_voltage+0.1)) {
  target_voltage = target_voltage + (looptime_seconds*accel);
}
if (goal_v < (target_voltage-0.1)) {
  target_voltage = target_voltage - (looptime_seconds*accel);
}
 for (int i = 0; i < 1000; i++){
  // main FOC algorithm function
  // the faster you run this function the better
  // Arduino UNO loop  ~1kHz
  // Bluepill loop ~10kHz 
  motor.loopFOC();

  // Motion control function
  // velocity, position or voltage (defined in motor.controller)
  // this function can be run at much lower frequency than loopFOC() function
  // You can also use motor.move() and set the motor.target in the code
  motor.move(-1*target_voltage);
 }
 if ((target_voltage >=1) && !underspeed_start && motor.shaftVelocity() > -5){ // it's in rads/s negative is the direction we are going. this is the stall detection
 underspeed_detect_start = millis();
 underspeed_start = true;
 }  
 if ( underspeed_start && motor.shaftVelocity() > -5){ // it's in rads/s negative is the direction we are going. this is the stall detection
 if ((millis() - underspeed_detect_start) > 5000){
 target_voltage = 0;
 goal_v = 0;
underspeed_start = false;

 }
 }
 if (motor.shaftVelocity() < -5){ // it's in rads/s negative is the direction we are going. this is the stall detection
  underspeed_start = false;
 }



 SerialComm();
}

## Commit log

2025-07-03 upload of stuff for posterity
    upload of stuff for posterity
    [anemometer mount v1.step, anemometer_mount1.3mf, anemometer_mount1.stl]
2025-07-03 Revert "upload of stuff for posterity"
    This reverts commit aa34602aeba9a9c387a14ca11f54fb902303c114.
    [anemometer mount v1.step, anemometer_mount1.3mf, anemometer_mount1.stl]
2025-07-03 Reapply "upload of stuff for posterity"
    This reverts commit e99ca66626acd12b2ef19132a99c6b6181bb32e5.
    [anemometer mount v1.step, anemometer_mount1.3mf, anemometer_mount1.stl]
2025-07-03 fan only and manometer stuff added
    added the fan only and the manometer stuff
    [bqfbn_num_4 v81 secondary.step, v16 extended v11 v2.step]
2025-07-08 initial update from tablet after fixing wifi issue
    [anemometer.py, main.py]
2025-08-17 cadr testing stuff various filter fan combos
    uploaded cadr teting stuff
    [bqap_bqfb_num_7 v18.f3d, bqap_bqfb_num_7 v18.step, bqfbn_num_4 v71.step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]
2025-08-21 backup thicker walls
    [asa_center_aug19_2025.step, frame only.step, grille only.step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]
2025-09-17 thicker blades for primary and secondary
    thicker blades for primary and secondary
    [primary thickerbladesfrom num10file_backup.step, secondary thickened_backup.f3d, secondary_thickened_backup.step]
2025-10-04 upload of manufacturing files mostly for backup
    [asa center.3mf, grillemoredense.3mf, trimmedframe.3mf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]
2025-10-13 Create How the Big Quiet Fan works better.rtf
2025-10-17 backup of step files
    [anemometer mount.step, asa_center.step, electronics box bottom.step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]
2025-11-09 stepper isolator cad backup
    this is the v2.0 which hasn't actualy been tested yet but it's very similar to the v1.0 which worked well
    [NEMA 23 stepper motor v1.step, motor dummy.step, secondary_thickened_16holes_combinedfromstep (v2~recovered).step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]
